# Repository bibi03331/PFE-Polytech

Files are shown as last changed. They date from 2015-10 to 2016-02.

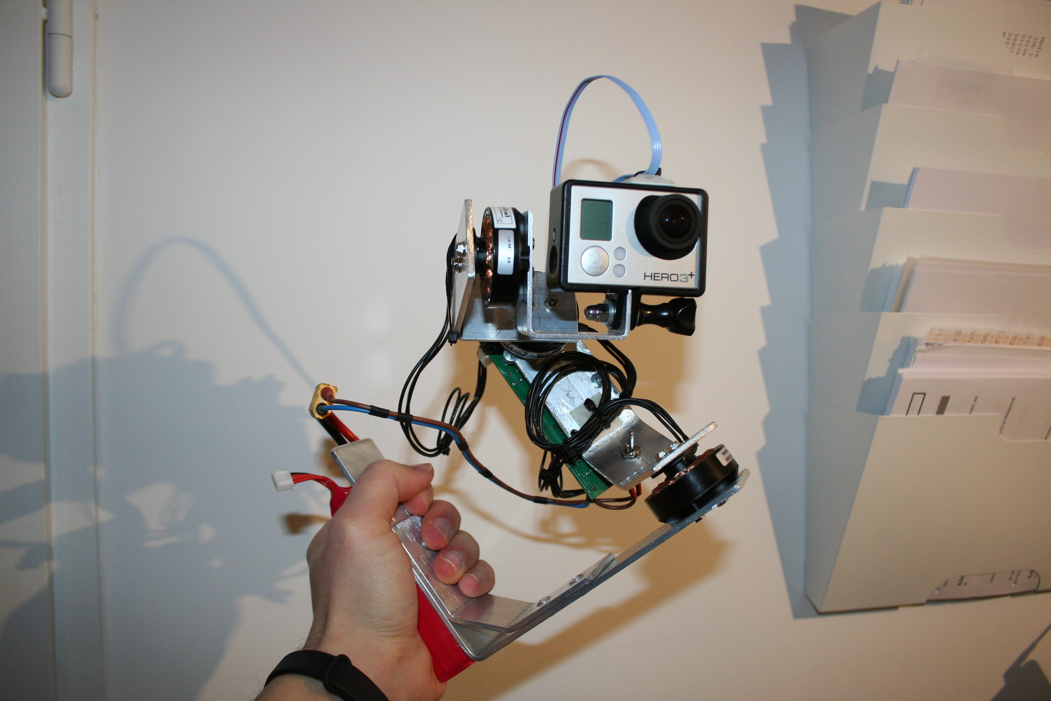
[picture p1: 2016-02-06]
Photos/Prototype final/IMG_9542.JPG

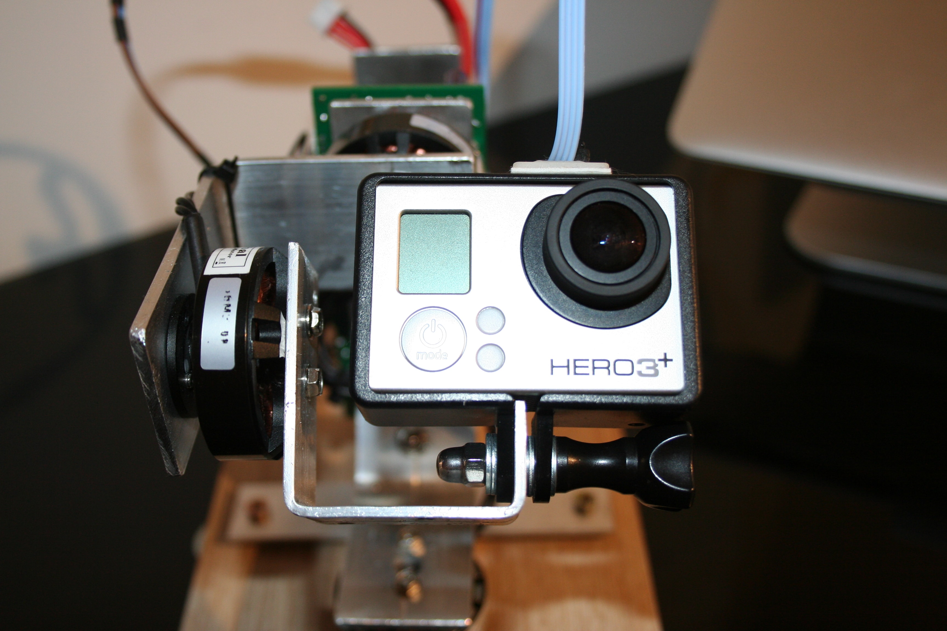
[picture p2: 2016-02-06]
Photos/Prototype final/IMG_9550.JPG

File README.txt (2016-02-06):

-------------------------------------------------------------
------------------ Projet de fin d'étude --------------------
------- Système de stabilisation motorisé pour caméra -------
-------------------------------------------------------------
       Réalisé par Sébastien Laporte à Polytech Tours
    Formation Informatique Industrielle par apprentissage
-------------------------------------------------------------

À la racine de ce dossier se trouvent l'ensemble des
livrables du projet.

  - Utilisateur : Un guide utilisateur est disponible dans
  ce dossier pour l'utilisation du système.

  - Administrateur : L'administrateur du système intervient
  pour ajuster les paramètres du système. Ce travail est
  nécessaire uniquement pour ajuster les paramètres en cas
  de modification de la structure mécanique, du type de
  moteur ou du type de caméra. Il a à sa disposition un
  guide administrateur et le code source du projet dont il
  aura besoin pour flasher à nouveau le programme dans le
  microcontrôleur avec les nouveaux paramètres

  - Développeur : Le développeur dispose de l'ensemble des
  codes sources mis à sa disposition dans le répertoire
  "Developpement" ainsi qu'un guide développeur.

-------------------------------------------------------------
==> Dossier "Developpement"
    Contient le programme du projet ainsi que l'ensemble des
    programmes réalisés au cours de ce projet.
=====> Dossier "Prototype initial"
       Contient les programmes Arduino réalisés au cours de
       la première partie du projet.
=====> Dossier "Prototype final"
       Contient les programmes Arduino réalisés au cours de
       la seconde partie de projet. Ils ont permis la
       réalisation et les tests pour le prototype final
=====> Dossier "Livrables"
       Contient les programmes Arduino mis en oeuvre pour
       la validation de chaque fonction tout au long du
       projet (Prototype initial et final). Ce dossier
       contient également la version finale du code et le
       répertoire pour la cross-compilation.
       Lien pour la mise en place de l'environnement de
       développement :https://www.pjrc.com/teensy/gcc.html
-------------------------------------------------------------

-------------------------------------------------------------
==> Dossier "CAO_mecanique"
    Contient les fichiers de conception mécanique de la
    structure et des éléments de protection.
=====> Dossier "Schémas"
       Contient les 3 schémas de la structure avant CAO
=====> Dossier "Plans et photos"
       Contient les mises en plan de chaque pièce du système
       ainsi que les aperçus des rendus 3D
=====> Dossier "Pièces"
       Contient les fichiers SolidWorks de chaque pièce
=====> Dossier "Impression 3D"
       Contient les fichiers .STL pour l'impression des
       boitiers de protection
-------------------------------------------------------------

-------------------------------------------------------------
==> Dossier "CAO_electronique"
    Contient les fichiers de conception électronique réalisés
    sous Multisim.
=====> Dossier "PDF"
       Contient le schéma de principe et les différentes
       couches du Typon
-------------------------------------------------------------

-------------------------------------------------------------
  ==> Dossier "Photos"
      Contient les photos réalisées au cours de la
      réalisation du projet
-------------------------------------------------------------

-------------------------------------------------------------
  ==> Dossier "Datasheets"
      Contient les datasheets des composants électroniques
      utilisés pour la partie électronique.
-------------------------------------------------------------

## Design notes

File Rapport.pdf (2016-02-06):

1

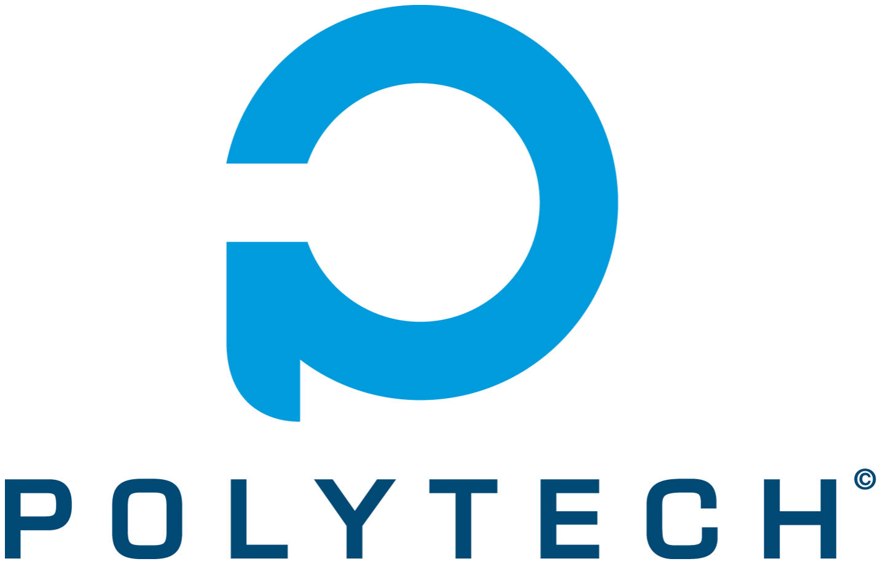
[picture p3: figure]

### École Polytechnique de l’Université de Tours

64, Avenue Jean Portalis
37200 TOURS, France
Tél. +33 (0)2 47 36 14 14

## www.polytech.univ-tours.fr

# Département Informatique industrielle

# Rapport de projet

Projet : | Système de stabilisation motorisé pour caméra
Réalisé par : | Sébastien LAPORTE | Encadré par : | Ameur SOUKHAL
Début du projet : | 22/09/2015 | Fin du projet : | 10/02/2015

Historique des modifications

Version | Date | Note de version
1.0 | 5/02/2016 | Version de dépôt initial

2

# Remerciements

Je tiens tout d’abord à remercier mon tuteur, Monsieur Ameur Soukhal pour ses conseils, et m’avoir suivi tout au long de ce projet de fin d’études.

Je remercie également les membres du service informatique de Polytech Tours et tout particulièrement Sébastien Beaufils pour sa disponibilité et son investissement. Monsieur Mayaud pour son aide et ses conseils avisés sur la réalisation de la partie mécanique du prototype. Monsieur Gaucher pour des conseils qu’il m’a apporté sur les technologies de capteurs.

Je tiens également à remercier l’ensemble des personnes qui ont contribué à la finalisation de ce rapport et de l’ensemble des documents établis.

Enfin, je tiens à remercier ma compagne pour avoir supporté de transformer ponctuellement la cuisine de notre appartement en atelier de soudure, de découpe et de perçage.

3

### Table des matières

4

## 1. Introduction

Ce document est un bilan de projet de fin d’études à Polytech Tours. Il a pour objectif de faire le lien entre les différents documents et livrables réalisés au cours de ce projet, d’exposer et justifier les choix qui ont été faits et d’effectuer un bilan sur le déroulement du projet.
Le porteur du projet qui agit également en tant que MOE est Sébastien Laporte, étudiant en cinquième année de cycle d’ingénieur en informatique industrielle. L’encadrant du projet représentant la MOA est Monsieur Ameur Soukhal, enseignant-chercheur au CNRS.
Le sujet du projet est la réalisation d’un système de stabilisation motorisé pour une caméra d’action sur trois axes.

## 1.1. Contexte du projet

Depuis quelques années, le marché des caméras d’action est en constante évolution. C’est la marque GoPro qui a démocratisé ce type de matériel et qui s’est imposée comme leadeur dans le domaine. Grâce à cette gamme de caméras, il est possible de filmer ses activités sportives, sur tous les terrains avec un minimum d’encombrement. Cependant, malgré la miniaturisation et la qualité du capteur, il est souvent difficile de filmer de manière stable lorsqu’on conduit une moto ou que l’on descend une piste de ski. C’est donc dans ce contexte que la MOA a proposé ce projet afin de trouver une solution à ce besoin.

## 1.2. Objectif

L’objectif de ce projet était de concevoir et réaliser un système de stabilisation pour caméra d’action. Fixée sur le système, la caméra sera stabilisée de façon mécanique pour permettre à l’utilisateur de filmer tout en conservant une image stable. Cette stabilisation sera assurée par des effecteurs électriques. Sont utilisation se devait simple et intuitive.

## 1.3. Existant

Certains projets ont vu le jour avec la prolifération des drones pourvus de caméras sur nacelles stabilisées. Le choix qui a été pris dans le cadre de ce projet est de considérer que le projet n’a pas d’existant ni matériel ni logiciel. En effet, dans le cadre pédagogique de ce projet, l’objectif était de se confronter à l’ensemble des problématiques mécaniques, électroniques et logicielles.

## 2. Cahier des charges

L’objectif du projet est de réaliser un système de stabilisation motorisé et autonome pour caméra. Usuellement appelé « Steady cam » pour « Steady camera », ce type de matériel est utilisé notamment dans le cinéma pour réaliser des travelings fluides en absorbant les mouvements parasites. Le système doit permettre d’assurer la stabilisation de caméras d’action type GoPro.
Contraintes du projet
- Le système doit être énergétiquement autonome
- La stabilisation doit se faire sur au moins deux axes : Roll + Pitch
- Effort de conception : Prototype avec un faible poids et encombrement
- L’utilisateur doit avoir la possibilité d’ajuster les paramètres d’amortissement

Livrables attendus
- Cahier de spécification
- Document d’analyse et modélisation
- Documentation de reprise de projet (Guide utilisateur, administrateur et développeur)
- Prototype fonctionnel

5

## 3. Problématique

Pour répondre aux spécifications qui ont été établies, nous avons établi la problématique suivante afin d’identifier les principales contraintes de ce système.
- Énergétiquement autonome
Le système doit être alimenté par batterie pour permettre à l’utilisateur de pouvoir l’utiliser sans contrainte d’alimentation secteur. Il est également nécessaire de prendre en compte le besoin important en courant pour l’alimentation de trois moteurs de façon simultanée.
- Réactivité
Destiné à stabiliser une caméra pour effectuer des prises de vue, le système doit être très réactif pour effacer les mouvements parasites induits par son utilisateur. Il est donc nécessaire d’avoir un traitement de l’information rapide, mais aussi d’avoir des effecteurs électriques suffisamment réactifs.
- Évolutivité
Dans le but de pouvoir modifier la structure mécanique pour l’adapter à un autre appareil de prise de vue, la partie électronique et la partie logicielle doivent être conçues pour s’adapter à ce changement. Cette contrainte implique un bon dimensionnement pour la partie électronique et une conception modulaire du programme afin de prévoir ces changements.
- Encombrement
Comme indiqué dans le cahier des charges, le système doit être le plus contenu possible afin de pouvoir être embarqué sur une moto, ou tenu à la main sans être une contrainte pour son utilisateur. Pour cela, un effort doit être fait sur la partie mécanique pour concevoir une structure la plus minimale possible. De plus, la partie électronique doit être parfaitement intégrée au système et respecter les mêmes dimensions que la structure.
- Robustesse
Enfin, la robustesse est un élément important à considérer. En effet, le produit doit être utilisable dans des conditions normales d’utilisation et doit être durable dans le temps. Cela implique une structure mécanique solide, des moteurs légèrement surdimensionnés ainsi qu’une protection des parties électroniques.

## 4. Conduite de projet

Pour mener à bien ce projet, nous avons dû sélectionner une méthode de gestion de projet. Ensuite, nous avons effectué un découpage des tâches pour réaliser un planning prévisionnel.
Notre choix de méthode s’est porté sur la méthode SCRUM des méthodes AGILE. En effet, étant sur des technologies que nous ne connaissions pas, le fait d’ajouter des fonctionnalités au système au fur et à mesure de l’avancement nous paraissait parfaitement adapté à ce projet.

## 4.1. Méthodologie

Comme présenté dans le livrable « Cahier de spécifications », nous avons organisé le projet en deux sous-projets. Cette décision a été faite après une étude de faisabilité au cours de laquelle nous avions identifié les risques. Le risque majeur de ce projet a été identifié comme l’obtention de l’orientation du capteur dans l’espace. En effet, aujourd’hui ces capteurs d’orientation intégrant un accéléromètre, un gyroscope et éventuellement un magnétomètre se trouvent dans tous les smartphones et tablettes du marché. Malgré le fait que ces capteurs soient très rependus, il y a encore très peu d’algorithmes Open Source permettant d’exploiter ces données. C’est pourquoi nous avons choisi dans un premier de nous consacrer à l’acquisition et au traitement des données sur un premier prototype. Puis, dans une deuxième phase du projet, après validation du fonctionnement de ces fonctionnalités de base,

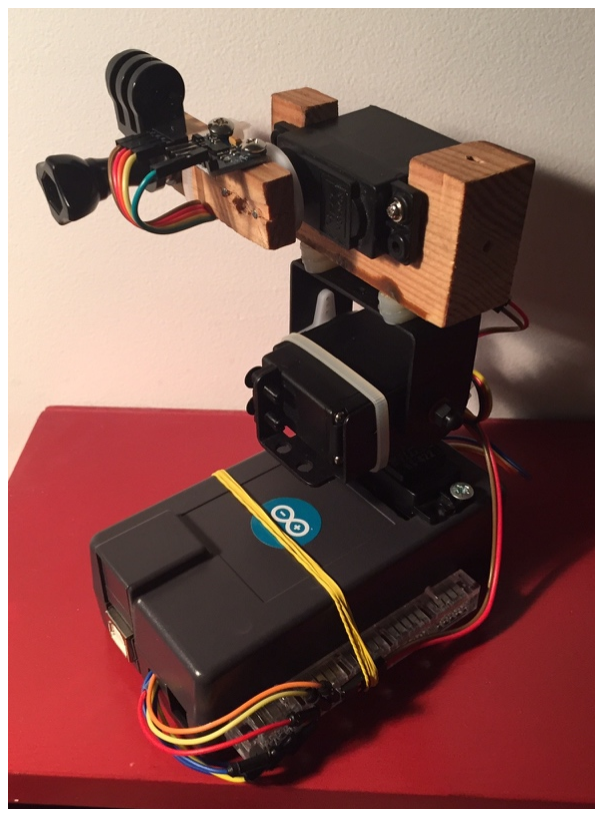
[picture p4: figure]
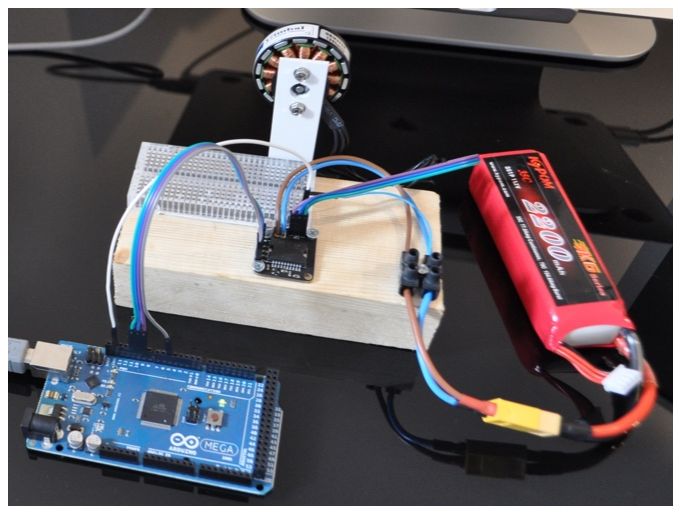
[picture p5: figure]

6

nous avions prévu de créer le prototype final, répondant à l’ensemble de la problématique et des exigences exprimées dans le cahier des charges.
- Prototype initial
Pour commencer le projet, nous avons choisi de nous
concentrer sur la prise en main du capteur et le traitement associé en mettant de côté la commande des moteurs brushless. Pour effectuer des tests, nous avons mis en place un prototype équipé de trois servomoteurs de modélisme pour remplacer les moteurs. En effet, la commande de ce type d’effecteur est grandement simplifiée par l’utilisation des librairies Arduino.
Ce premier prototype a permis de mettre en œuvre :
- La configuration du capteur
- De comprendre et d’implémenter un algorithme permettant d’effectuer la calibration du capteur
- D’implémenter un algorithme de filtre PID
- De tester plusieurs techniques de fusion de données d’un tel capteur
- De valider le fonctionnement du prototype sur deux axes : Roll et Pitch
Après la validation de fonctionnalités, nous avons réalisé
des vidéos pour valider le fonctionnement auprès de la
MOA :
- Prototype initial sur deux axes : https://www.youtube.com/watch?v=oEspsLbolnE
- Ajout de l’axe Z (Yaw) : https://www.youtube.com/watch?v=FzccmuE41do
- Prototype initial sur trois axes : https://www.youtube.com/watch?v=J3hMNFk_600

Dans cette première partie, nous avons également
réalisé un banc d’essai moteur pour prendre en
main la commande de ce type de moteur brushless et implémenter la fonction permettant la commande.
Pour réaliser la commande du moteur, nous avons utilisé une Breadboard intégrant le composant L6234 afin de concentrer le travail sur l’implémentation de la fonction au niveau du microcontrôleur. La partie électronique sera mise en œuvre pour le prototype final.
Le fonctionnement de la commande d’un moteur
brushless a également été validé avec un vidéo
comme livrable. Celle-ci montre le fonctionnement du moteur avec variation de la vitesse : https://www.youtube.com/watch?v=QIOnZgU_zDE À la fin de cette première partie du projet, nous avions mis en œuvre l’ensemble des techniques nécessaire à la réalisation du prototype final.

Figure 1 : Prototype initial

Figure 2 : Banc d'essai moteur

7

- Prototype final
La seconde partie du projet a pour objectif de capitaliser les connaissances et techniques développées lors de la première partie du projet pour les intégrer dans un prototype final. Dans cette partie du projet, nous avions donc toutes les connaissances nécessaires à la conception et à la réalisation du système.
Lors de cette phase, nous avons effectué la conception de la carte électronique, la conception mécanique et le code optimisé pour le microcontrôleur sélectionné pour le prototype final.

## 4.2. Découpage en tâches

Le découpage en tâches a été réalisé dans la partie 8 du livrable « Cahier de spécifications ».

## 4.3. Choix stratégiques

Au cours du projet, nous avons dû effectuer des choix techniques qui sont liés à la gestion de projet.
- Choix de l’algorithme de fusion des données du capteur
Pour obtenir l’orientation d’un solide dans l’espace il existe plusieurs types de capteurs. Dans le cadre de ce projet, nous avions établis lors de la phase de spécification d’utiliser un accéléromètre, un gyroscope et un magnétomètre. Pour obtenir l’orientation du solide, il est nécessaire de fusionner ces valeurs afin d’obtenir par exemple une représentation d’Euler. Lors de nos recherches, nous avions observé qu’il existe essentiellement deux méthodes pour obtenir l’orientation avec le capteur mPU-9250 :
- Soit utiliser le DMP (processeur spécialisé dans le calcul intégré au capteur). Cette Solution permet d’obtenir de manière simple et précise l’orientation du capteur.
- Soit mettre en œuvre un algorithme au niveau du microcontrôleur en récupérant les valeurs brutes des différents capteurs. Cette solution nécessite l’utilisation d’un algorithme mathématique déjà existant, car cela requiert de grandes compétences très spécialisées.
La solution avec l’utilisation du DMP n’a pas été retenue du fait de devoir flasher à chaque démarrage du système le code binaire d’un programme propriétaire dans le DMP. En effet, nous avions comme volonté de maitriser l’ensemble des fonctions que nous utilisons pour ce projet. Nous avons donc choisi d’implémenter l’algorithme de Madgwick au niveau du microcontrôleur. Nous verrons par la suite que ce choix n’a pas permis d’aboutir à une solution pleinement satisfaisante en terme de performances.
- Choix sur la structure mécanique
De nombreuses structures avec moteur brushless intégrés sont en vente dans des boutiques spécialisées ou sur internet. Ces Structures sont destinées à être utilisées sur des drones pour stabiliser des caméras d’action. Ce type de matériel aurait très bien pu convenir pour ce projet. Néanmoins, ayant des connaissances en conception mécanique, nous avions comme volonté de réaliser nous même l’ensemble dans la partie mécanique.
- Choix sur la partie électronique
Comme pour la partie mécanique, le marché des drones a fait apparaitre des cartes électroniques intégrant un microcontrôleur, des drivers de moteurs brushless sur une même carte pour un encombrement et un prix très réduit. Là encore, nous souhaitions réaliser nous même notre propre carte électronique afin de nous confronter aux différentes problématiques induites par ce type de projet.

8

## 4.4. Planification

La gestion du planning établie en début de projet (voir cahier de spécification, partie 10) a été suivie à quelques exceptions en fin de projet en raison de tests non satisfaisants sur une tâche du projet qui nous a contraints à revenir sur l’implémentation d’une fonction. Certaines tâches non prioritaires n’on donc pas pût être réalisées :
- Réalisation du code natif pour la fonction « Commande de l’orientation »
- Intégration du code natif pour le prototype final
Nous avions environ 120h dédiées sur notre emploi du temps pour la réalisation du PFE. Pour mener à bien ce projet, nous avons consacré entre 470 et 500 heures ce qui totalise un minimum de 450 heures sur le temps personnel. Cet investissement personnel nous a permis de ne pas prendre de retard sur le planning que nous nous étions fixé.

## 4.5. Livrables du projet

Ce rapport est accompagné de plusieurs livrables détaillants les spécifications et l’analyse qui a été faite pour ce projet. Les guides doivent permettre une reprise du projet par niveau d’utilisateur.
- Cahier de spécifications
Ce document a pour objectif de définir les besoins, l’environnement et les objectifs pour la réalisation du projet. Il contient le découpage des tâches ainsi que la planification.
- Document d’analyse et modélisation
Ce document a pour objectif d’expliquer en détail les choix et solutions mises en place pour la réalisation du projet de fin d’études. Ce rapport est organisé en plusieurs sous-parties : Électronique, mécanique et logicielle.
- Guide de l’utilisateur
Ce document est destiné à l’utilisateur du système. Il décrit les démarches à suivre pour l’utilisation du système.
- Guide l’administrateur
Ce document est destiné à l’administrateur du système. Il décrit les démarches à suivre pour la configuration du système. Les configurations présentées dans ce document doivent être effectuées par l’administrateur pour préparer le système après sa fabrication. Ce paramétrage est à effectuer une seule fois dans la vie du système. Ce document peut être également utile aux développeurs.
- Guide du développeur
Ce document est destiné à décrire l’architecture du code et présente les différents codes sources associés au projet.
- Code source du projet
Ce projet est livré avec le code source et son environnement nécessaire à la cross-compilation.
- Codes exemples associés au projet
L’ensemble des codes sources des programmes utilisés au cours de la vie du projet est également inclus dans les livrables du projet. Ils sont décrits dans le guide du développeur.

9

## 5. Schéma général du système

Le schéma ci-dessous permet de définir le nom des axes que nous avons utilisé dans l’ensemble des rapports et documents fournis. Il permet également de définir le repère géométrique.

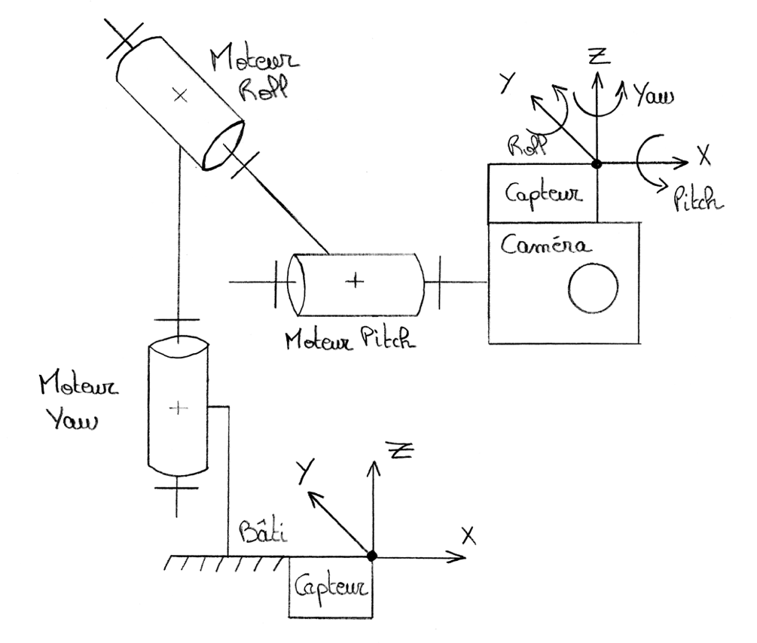
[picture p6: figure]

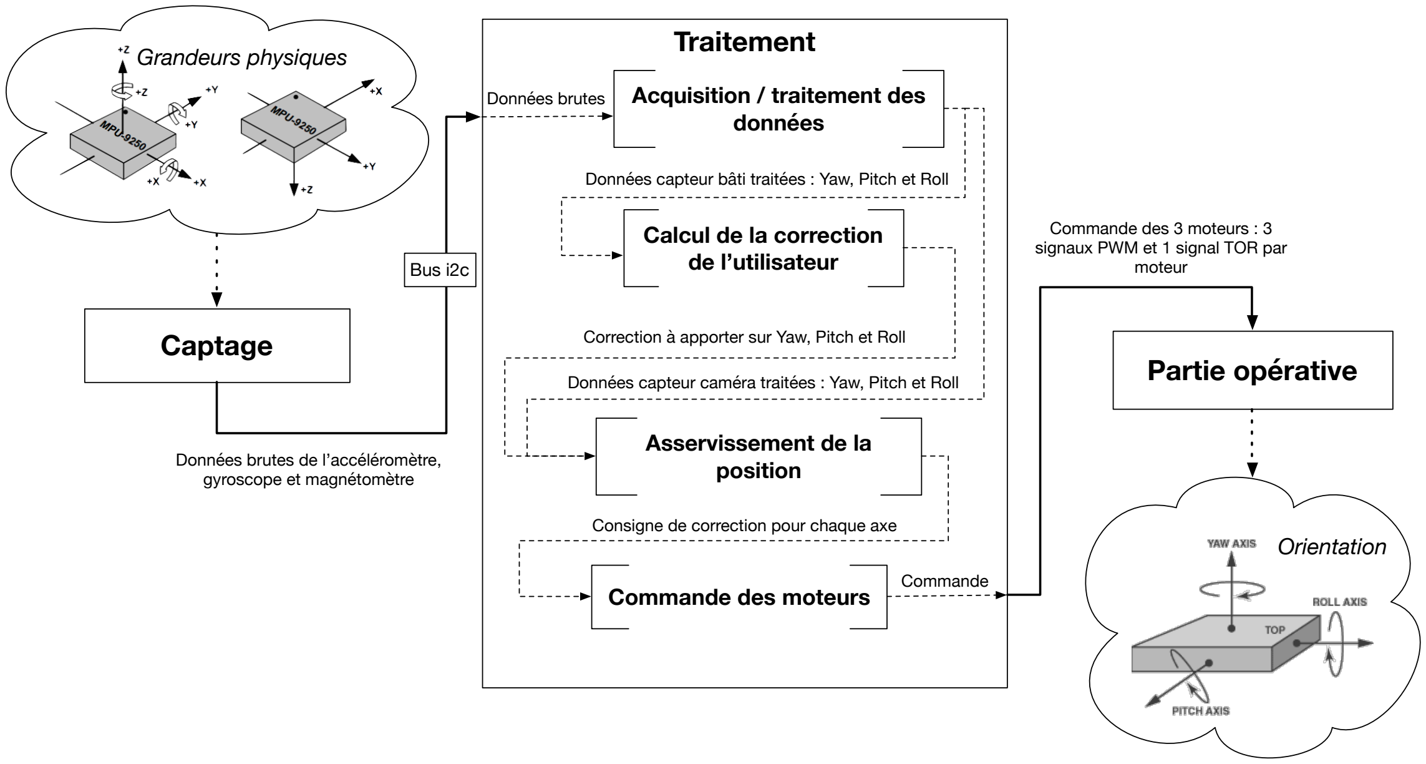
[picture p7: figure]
Captage; Traitement; Acquisition / traitement des données; Asservissement de la position; Commande des moteurs; Partie opérative; Grandeurs physiques; Bus i2c; Données brutes de l’accéléromètre, gyroscope et magnétomètre; Consigne de correction pour chaque axe; Données brutes; Commande; Commande des 3 moteurs : 3 signaux PWM et 1 signal TOR par moteur; Orientation; Calcul de la correction de l’utilisateur

10

## 6. Architecture mise en œuvre

Pour réaliser la fonction de stabilisation de la caméra, nous avons découpé le système en trois sous-parties : Captage, Traitement et partie opérative.

Figure 4 : Architecture du système
Ø Captage : Sous-ensemble permettant de fournir au système les données brutes nécessaires à la modélisation de l’orientation de la caméra et du système dans un espace 3D. C’est grâce à l’orientation de la caméra que nous effectuons l’asservissement en position.
Ø Traitement : Sous-ensemble permettant de réaliser plusieurs fonctions : Traitement des données, calcul de la correction de l’utilisateur, asservissement en position et commande des moteurs.
- Fonction « Acquisition / traitement des données » : Permets d’obtenir l’orientation exacte de la caméra et du bâti à partir des données brutes envoyées par le sous-ensemble « Captage ».
- Fonction « Calcul de la correction de l’utilisateur » : Cette fonction permet de calculer la correction à apporter pour modifier l’orientation de la caméra en fonction de celle du bâti.
- Fonction « Asservissement de la position » : Permets de calculer la correction à appliquer sur le sous-ensemble « Partie opérative » pour corriger l’orientation de la caméra en fonction des données produites par la fonction « Traitement des données ».
- Fonction « Commande des moteurs » : Permets d’effectuer la commande des moteurs en fonction de la consigne calculée par la fonction « Asservissement de la position ».
Ø Partie opérative : Sous-ensemble constitué d’une structure mécanique et de moteurs permettant d’orienter la caméra dans un espace 3D.

Données capteur caméra traitées : Yaw, Pitch et Roll

Données capteur bâti traitées : Yaw, Pitch et Roll

Correction à apporter sur Yaw, Pitch et Roll

11

## 7. Matériel utilisé

Le choix et la justification des composants du système a été réalisé dans le livrable « Analyse et modélisation » dans la partie 4.1. La liste de matériel qui suit concerne le matériel nécessaire à la réalisation du prototype final. Au cours du projet, un premier prototype à été réalisé qui sera décrit dans la partie gestion de projet.
Le tableau ci-après fait une synthèse du matériel qui a été nécessaire à la réalisation électronique.
Désignation | Quantité | Prix unitaire TTC
Capteur MPU-9250 | 1 | 11,90€
Moteur brushless BLDC GBM3508-130 | 3 | 24,43€
Microcontrôleur Teensy 3.1 | 1 | 19,80€
Batterie LIPO 3S 2200 mAh | 1 | 23,90€
Régulateur LM2574 | 3 | 7,80€
Support DIP20 | 3 | 1,03€
Condensateur chimique 22 uF | 1 | 0,50€
Condensateur chimique 220 uF | 1 | 0,80€
Condensateur céramique 100 nF | 3 | 0,10€
Condensateur chimique 100 uF | 3 | 0,50€
Condensateur céramique 220 nF | 3 | 0,80€
Diode Schottky MBR160G | 1 | 0,20€
Bobine 330 uH | 1 | 1,00€
Condensateur céramique 10 nF | 3 | 0,10€
Condensateur céramique 1 uF | 3 | 0,10€
Diode 1N4148 | 6 | 0,10€
PCB Eurocircuit | 1 | 71,91€
Interrupteur 2 positions | 1 | 2,90€
Total TTC | 238,39€

Le tableau ci-après constitue la la liste du matériel pour la réalisation de la partie mécanique.
Désignation | Quantité | Prix TTC
Plat aluminium brut (Longueur 1 m – Largeur 35 mm) | 1 | 7,45€
Plat aluminium brut (Longueur 1 m – Largeur 20 mm) | 1 | 5,90€
Vis M3 15 mm à tête cylindrique + écrous + rondelles | 4 | 2,00€
Vis M3 5 mm à tête plate | 9 | 2,00€
Fixation GoPro « The Frame » | 1 | 9,90€

Coût total du projet en matériel : 265,64€

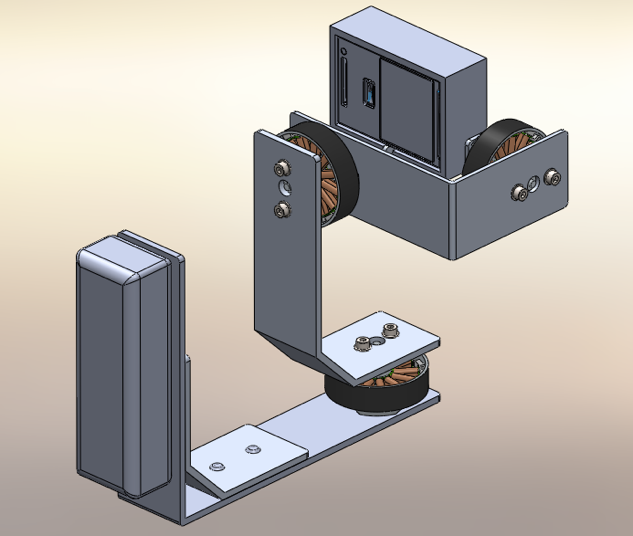
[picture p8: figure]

12

## 8. Conception et réalisation

## 8.1. Conception de la structure

Afin de réaliser la structure mécanique, nous avons réalisé dans un premier temps un schéma permettant de définir les éléments de la structure.

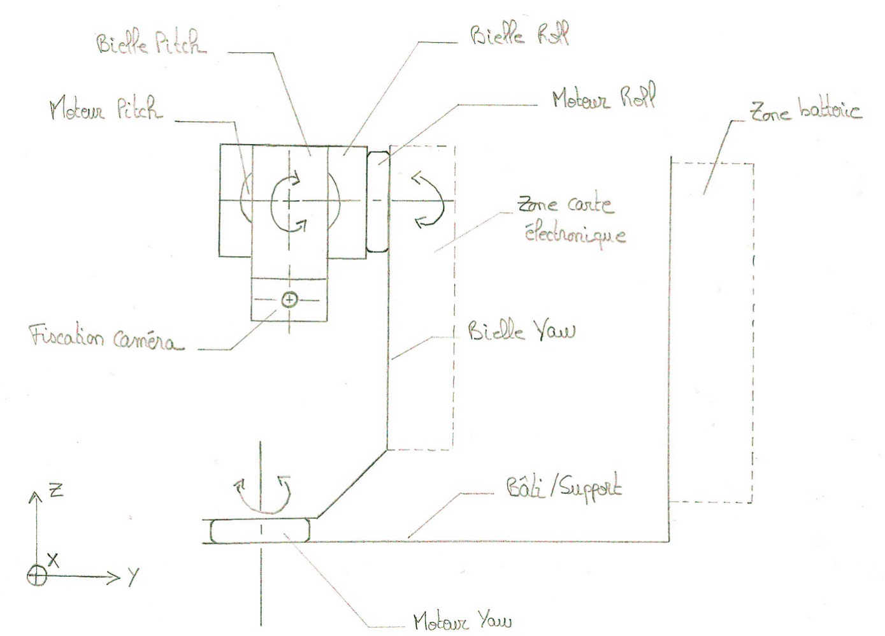
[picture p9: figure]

Figure 5 : Schéma de la structure mécanique
Nous avons ensuite entrepris une phase de conception sur ordinateur à l’aide du logiciel SolidWorks pour obtenir un 3D. Cela a également permit de définir les dimensions exactes de chaque pièce et de s’assurer qu’il n’y a pas de collisions entre les différents éléments. Les plans de l’ensemble de la structure se trouvent en annexe du document « Analyse et modélisation ».

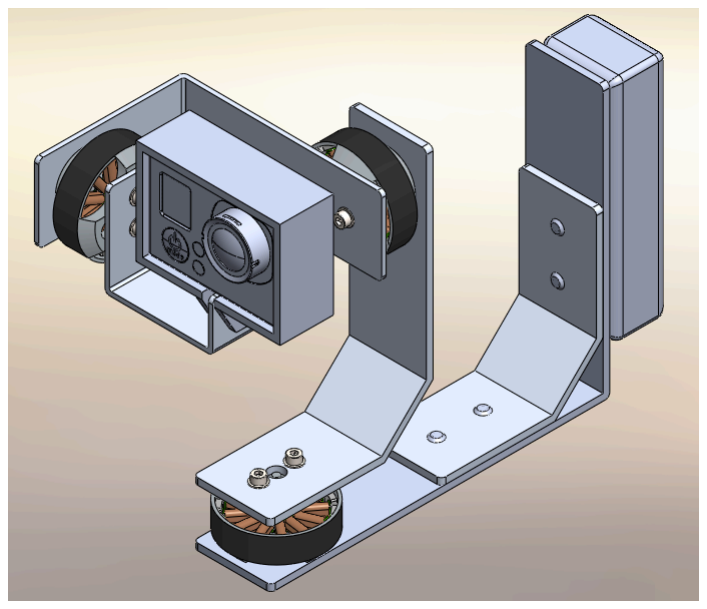
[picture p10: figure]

Figure 6 : Rendu 3D structure mécanique

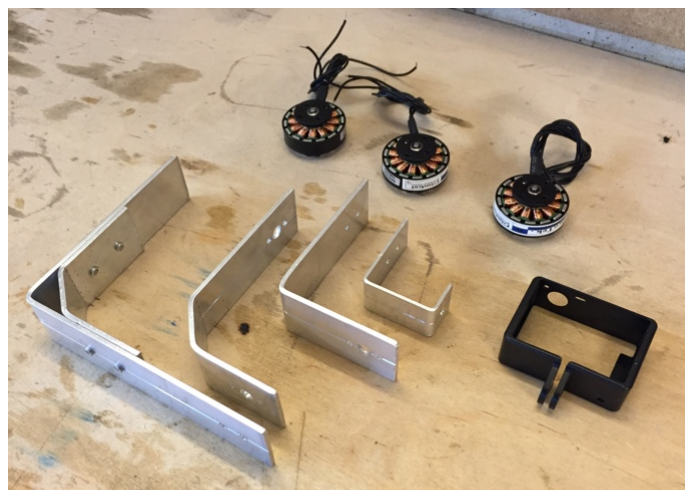
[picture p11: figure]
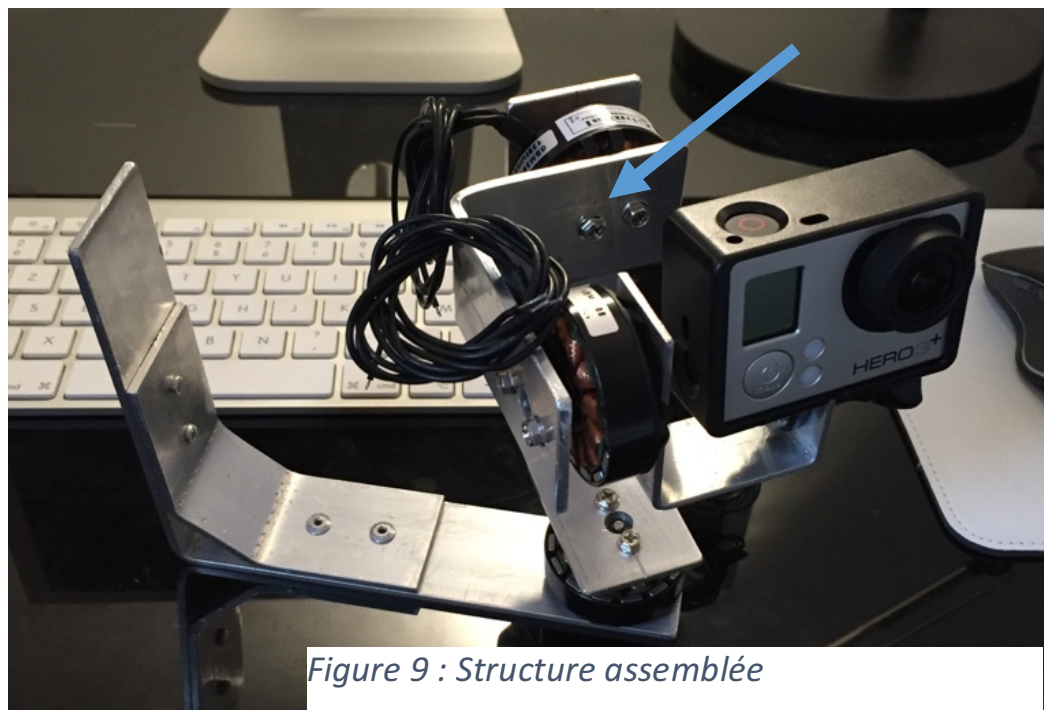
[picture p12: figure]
Figure 9 : Structure assemblée

13

## 8.2. Conception des éléments de protection

Afin de protéger la carte électronique, nous avons réalisé un boitier de protection. Nous avons effectué la conception sur ordinateur, puis réalisé les pièce grâce à une imprimante 3D.

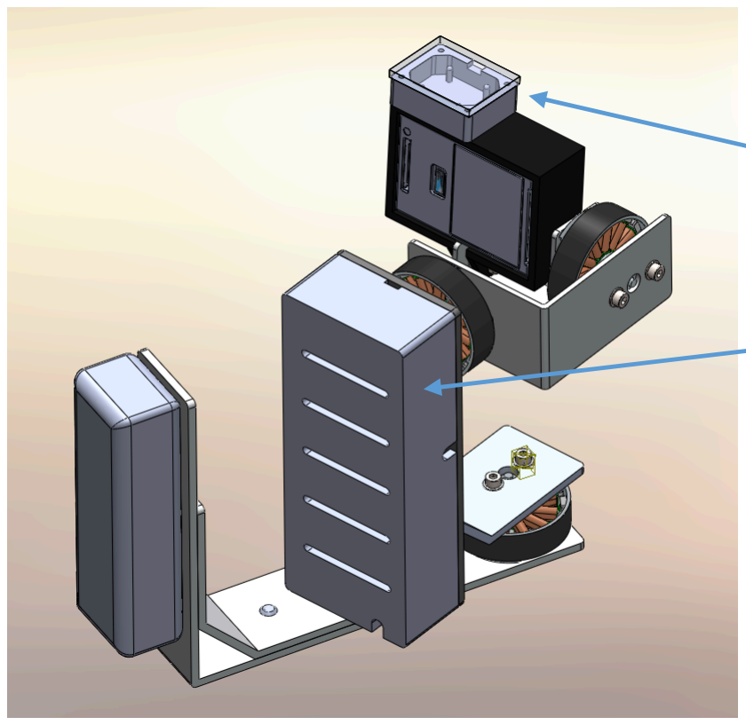
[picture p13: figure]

Figure 7 : Éléments de protection

## 8.3. Réalisation de la structure

Pour réaliser la structure mécanique, nous nous sommes appuyé entièrement sur les plans que nous avions réalisé pour chaque pièce grâce à la modélisation 3D. En procédant ainsi, nous avions l’assurance de réaliser les pièces avec les bonnes dimensions.
Cependant, lors de la modélisation nous n’avions pas les compétences nécessaires pour prendre en compte le poids de la caméra pour calculer le point d’équilibre de la structure.

En effet, comme on le voit sur l’illustration ci-contre, le système est en équilibre, même sans l’aide des moteurs. Cela permet d’éviter aux moteurs d’appliquer un effort lorsque le système est parfaitement à l’horizontal. Nous avons donc dû adapter la dimension de la bielle pointée par la flèche sur l’illustration afin d’obtenir le résultat suivant.

Boitier de protection du capteur

Boitier de protection de
la carte électronique

Figure 8 : Réalisation de la structure

## 8.4. Partie électronique

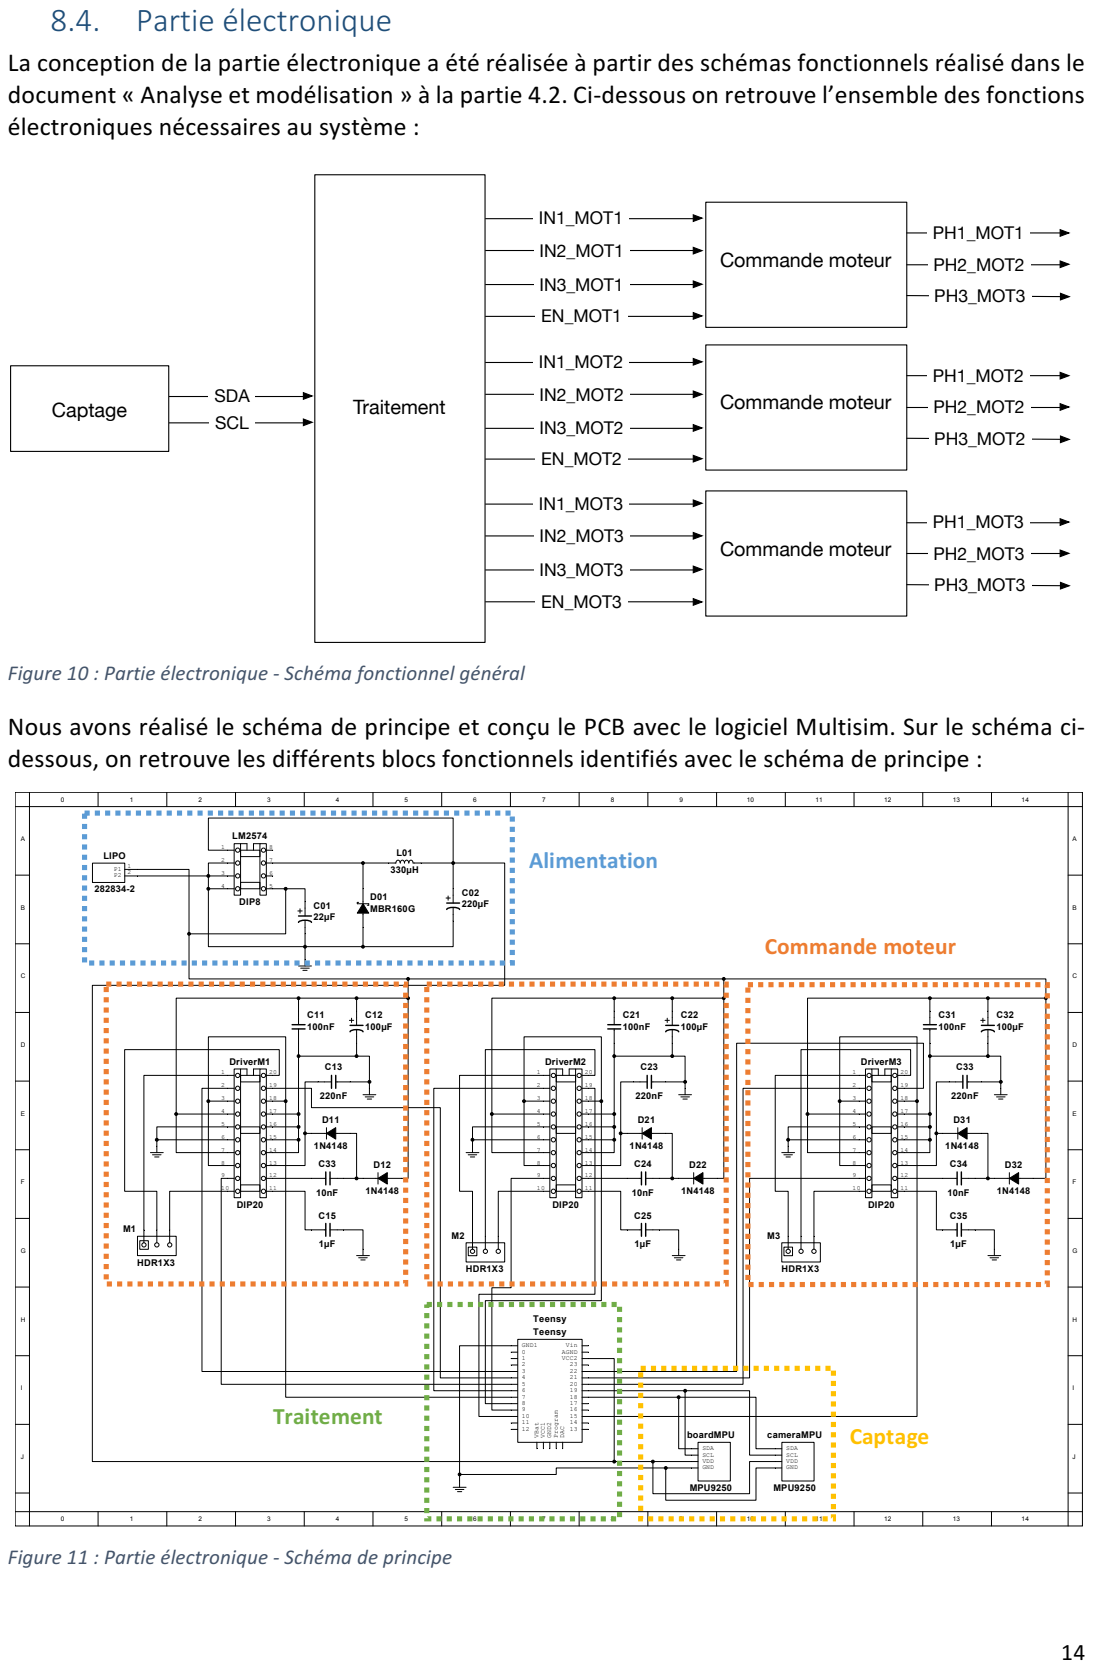
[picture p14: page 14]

La conception de la partie électronique a été réalisée à partir des schémas fonctionnels réalisé dans le
document « Analyse et modélisation » à la partie 4.2. Ci-dessous on retrouve l’ensemble des fonctions
électroniques nécessaires au système :

Figure 10 : Partie électronique - Schéma fonctionnel général
Nous avons réalisé le schéma de principe et conçu le PCB avec le logiciel Multisim. Sur le schéma ci-
dessous, on retrouve les différents blocs fonctionnels identifiés avec le schéma de principe :

Figure 11 : Partie électronique - Schéma de principe

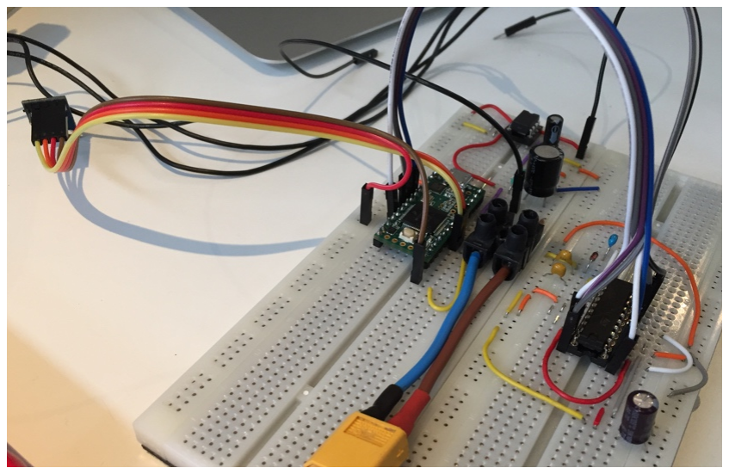
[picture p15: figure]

15

Pour valider cette conception que nous avions réalisée en nous appuyant sur les datasheet des composants, nous avons utilisé une platine de développement reproduit chaque fonction.
Ainsi, nous avons pu valider chaque
fonction | électronique
indépendamment en réalisant un
programme | de | test | sur | le
microcontrôleur. Après la validation de chaque fonction, nous avons effectué un test avec l’ensemble des
fonctions pour nous assurer qu’il n’y
a pas d’effet de bords.
La contrainte principale pour la conception de la carte électronique était l’encombrement. En effet, nous devions contenir au maximum les dimensions du PCB pour qu’il puisse être fixé sur le système sans gêner l’utilisateur.

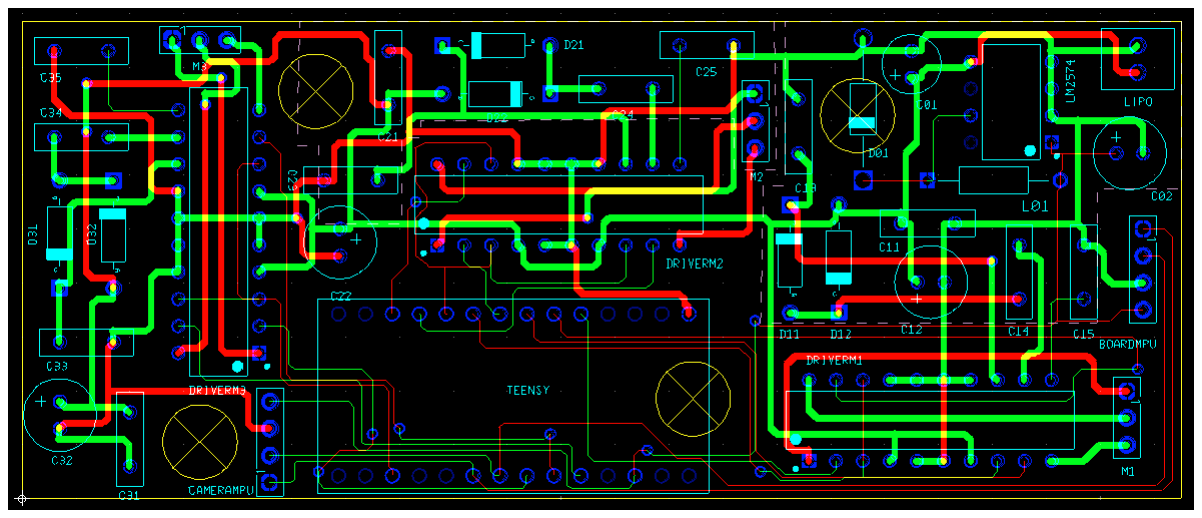
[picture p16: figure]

Figure 13 : Partie électronique - Conception du PCB
Le PCB a été réalisé en 2 couches pour permettre un gain de place. Toujours dans une démarche d’optimisation, nous avons utilisé deux tailles de piste :
- Les pistes de données : 0,254 mm
- Les pistes de puissance : 0,762 mm Afin de limiter les perturbations électromagnétiques entre les pistes de puissance et les pistes de données, nous avons créé des zones « keep-out » pour éloigner au maximum de deux types de pistes. Le placement des composants a également nécessité un travail d’optimisation pour trouver l’arrangement qui permet un encombrement minimum tout en limitant les proximités de certaines pistes et en rapprochant au maximum les condensateurs de découplages des composants concernés. Le PCB a été réalisé par la société EURO circuits. Afin de supporter les forts courants induits par les moteurs, nous avons spécifié une épaisseur de piste à 35μm pour supporter les forts courants.

Figure 12 : Conception électronique - Tests

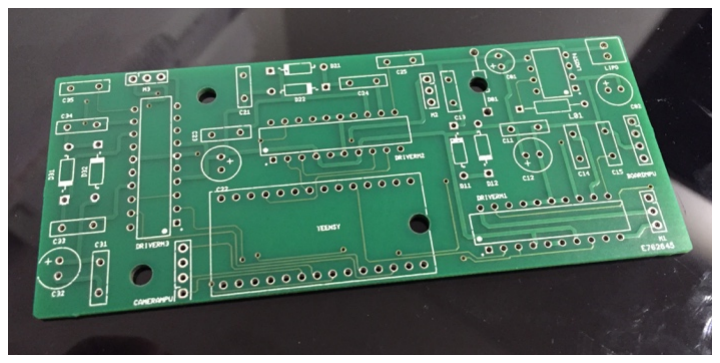
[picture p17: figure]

16

Afin de pouvoir fixer efficacement la carte électronique à la structure mécanique, nous avions prévu des trous de fixation lors de la conception du PCB.
Afin d’obtenir un PCB de qualité et de simplifier la soudure des composants, nous avons opté pour une finition « Standard Pool » ce qui permet d’avoir une carte vernie (meilleur durée
de vie) et des trous métallisés pour les
composants.
La dernière étape de pour la partie électronique à été la mise en place des composants sur le PCB et le test de chaque partie. Pour effectuer les tests, nous avons connecté les trois moteurs ainsi que le capteur à la carte et avons flashé sur le microcontrôleur un programme permettant de faire l’acquisition des données brutes du capteur tout en faisant tourner les trois moteurs.
L’ensemble des tests ont étés réalisés avec succès.

Figure 14 : Partie électronique - PCB

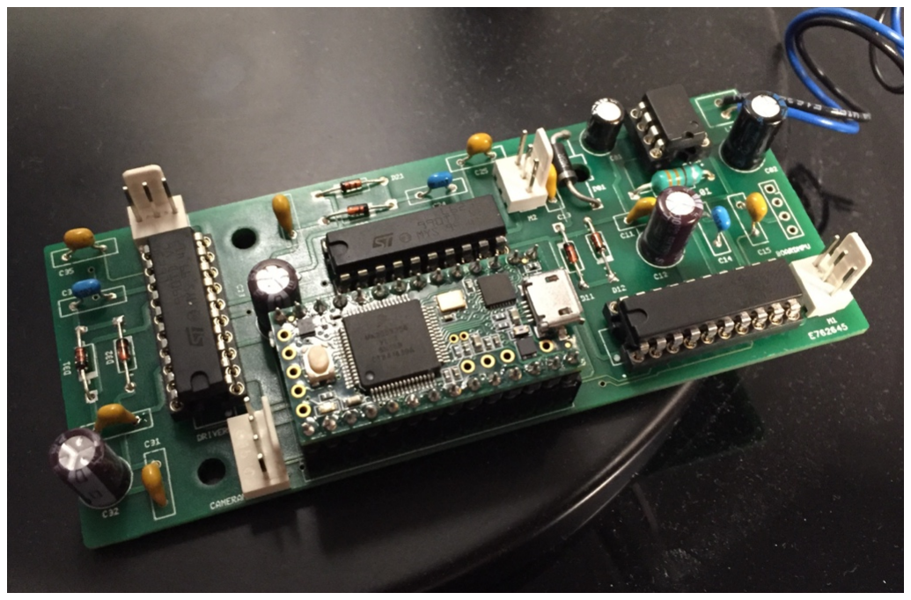
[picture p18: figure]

Figure 15 : Partie électronique - Carte électronique assemblée

17

## 8.5. Partie logicielle

Le programme du microcontrôleur est organisé en deux partie :
- Une phase d’initialisation permet de configurer le matériel, charger les paramètres et éventuellement d’effectuer l’étalonnage du capteur. Cette phase est décrite dans le document « Analyse et modélisation » dans la partie 6.5.1.
- La phase de fonction normal permet d’effectuer la stabilisation de la caméra. Le processus est constitué d’un ensemble de fonctions qui s’enchainent de façon séquentielle. Cette phase est décrite dans le document « Analyse et modélisation » dans la partie 6.5.2.
8.5.1. Phase d’initialisation du programme

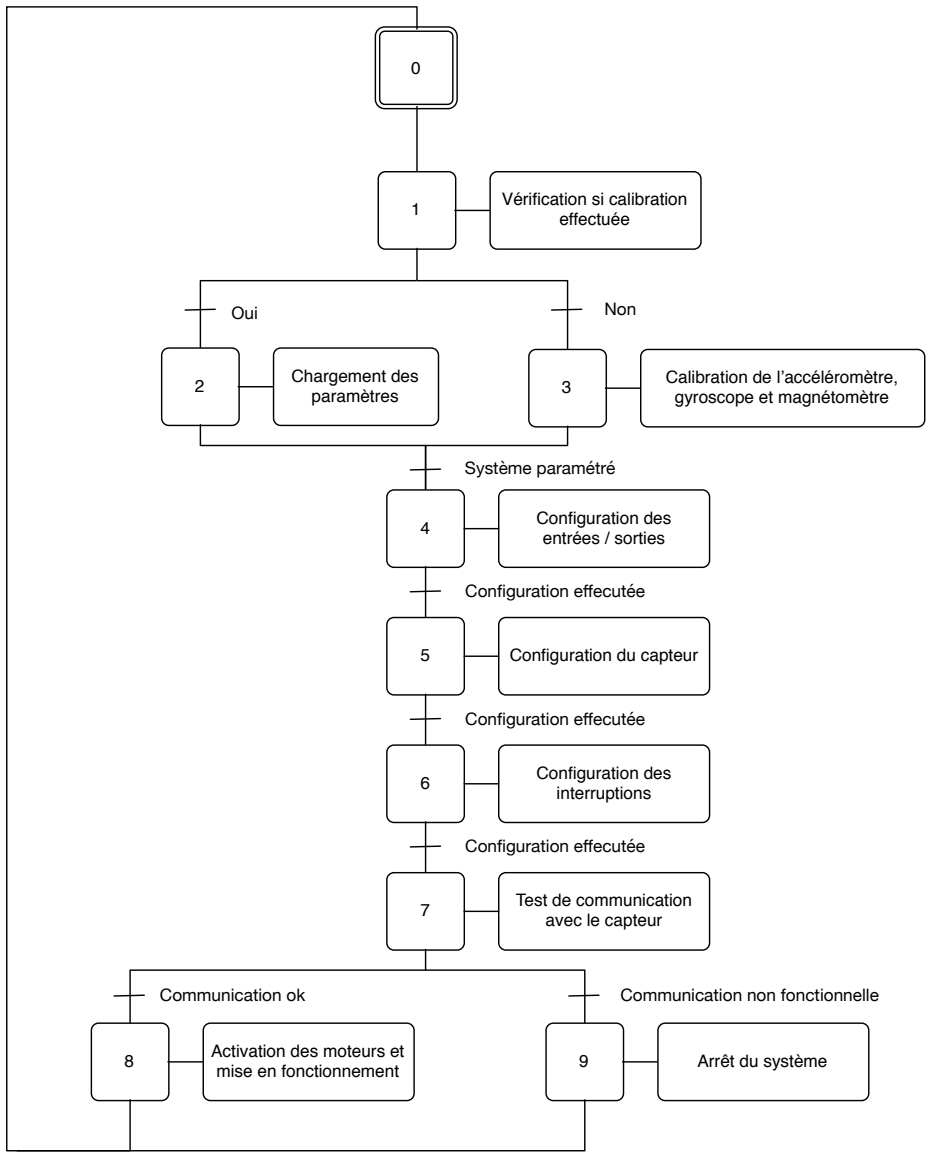
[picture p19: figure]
Vérification si calibration; effectuée; Calibration de l’accéléromètre,; gyroscope et magnétomètre 2; Chargement des; paramètres; Oui; Non; Configuration des; entrées / sorties; Configuration du capteur; interruptions; Test de communication; avec le capteur; mise en fonctionnement; Communication ok; Communication non fonctionnelle; Système paramétré; Configuration effecutée

Figure 16 : Partie logicielle - Phase d'initialisation

8 | 9 | Arrêt du système Activation des moteurs et

18

8.5.2. Phase de fonctionnement normal du programme Le processus de fonctionnement normal du programme du microcontrôleur peut être décrit par le grafcet ci-contre. Les fonctions représentées s’enchaines successivement en partant de la récupération des données brutes du capteur jusqu’à la commande de la partie opérative. Cependant, les opérations sont cadencées par des interruptions avec les fréquences suivantes :
Interruption 1 : Cadencée à 200 Hz
- Récupération des données brutes du capteur
- Conversion de la représentation quaternion en Euler

Interruption 2 : Cadencée à 50 kHz
- Application du filtre PID
- Commande de la partie opérative

Interruption 3 : Cadencée à 1 kHz
- Application du filtre de Madgwick

Pour plus de détails sur le cadencement de ces interruptions, se référer à la partie 6.5.2 du livrable « Analyse et modélisation ».

8.5.3. Configuration du capteur
Durant ce projet, une des tâches qui nous aura pris le plus de temps est la configuration du capteur. En effet, le capteur MPU-9250 est très complexe et dispose d’un grand nombre de registres pour effectuer sa configuration. De plus, sa configuration fait appel à des notions de physique que nous ne maitrisions pas en début de projet, et qui restent relativement abstraites malgré un important travail de recherche. Dans la partie 6.4.1 du livrable « Analyse et modélisation », nous avons décrit avec précision les registres du capteur à configurer et la démarche à adopter pour mettre en œuvre le bon fonctionnement de ce capteur. La calibration est également un point très important pour obtenir des valeurs fiables. Nous avons également expliqué les étapes à effectuer pour correctement calibrer le capteur dans le document d’analyse dans la partie 6.4.3.1 et 6.4.3.2.
8.5.4. Mise en œuvre des moteurs brushless BLDC
Ce type de moteur est particulièrement intéressant dans son fonctionnement. Il permet un positionnement extrêmement précis (résolution de 0,1°) sans utiliser de codeur ou de capteur à effet hall. Ainsi, on peut effectuer un asservissement très précis avec ces moteurs avec une grande réactivité ce qui correspond parfaitement à la problématique du système. La mise en œuvre du programme a été facilitée par de nombreux exemples trouvés sur internet. De plus, l’algorithme permettant de commande ce type de moteur est relativement simple en utilisant un « lookup-table ». Cette table contient l’ensemble des trinômes de valeurs des signaux PWM à appliquer aux entrées du moteur. Ainsi, pour faire tourner le moteur, il suffit de se déplacer dans la table.
Cette technique de « Lookup table » permet d’éviter d’effectuer des calculs au niveau du microcontrôleur. Pour effectuer les premiers tests, nous avons dans un premier temps généré une
1 | Récupération des données brutes du capteur

0

2 | Application du filtre de Madgwick
3 | Conversion de la représentation quaternion en Euler
4 | Application du filtre PID
5 | Commande de la partie opérative

Figure 17 : Partie logicielle - Fonctionnement normal

19

table contenant 71 valeurs. Les moteurs utilisés possèdent 7 trinômes d’enroulements ce qui permet d’obtenir 497 pas pour 360 degrés ce qui représente une précision de 0,72 degré. Pour augmenter la précision, il suffit de générer plus de valeurs (avec une limite de 255 valeurs : résolution des PWM configurées sur 8 bits).
Pour éviter les perturbations sonores liées à la fréquence des signaux PWM, nous avons augmenté la fréquence à 18 kHz, ce qui est inaudible à l’oreille humaine. Dans certains exemples observés lors de nos recherches sur internet, la fréquence était fixée à 32 kHz. Nous avons jugé qu’une fréquence plus basse produirait le même effet en terme d’atténuation des nuisances sonores. De plus, une fréquence de fonctionnement moins élevée permet d’éviter l’échauffement des moteurs et par conséquent, la consommation énergétique du système.
8.5.5. Exploitation des données du capteur
Afin d’obtenir l’orientation du capteur dans l’espace, nous avions sélectionné la solution qui est d’utiliser l’algorithme de Madgwick. Cet algorithme, créé par un étudiant de l’université de Bristol, permet la fusion des données d’un accéléromètre, du gyroscope et d’un magnétomètre pour obtenir l’orientation sous la forme d’un quaternion. Pour effectuer l’asservissement de notre système, nous utilisons la représenter d’Euler. Une formule mathématique permet de passer d’un quaternion à Euler. Cet algorithme Open Source est utilisé dans notre programme comme une boite noire à laquelle on transmet les valeurs brutes du capteur. En retour, nous obtenons un quaternion qui peut être exploité par la suite en passant à la représentation d’Euler.
Pour plus d’informations sur l’algorithme de Madgwick : http://www.x-io.co.uk/open-source-imu-and-ahrs-algorithms/
8.5.6. Asservissement en position
L’asservissement en position est réalisé par un filtre PID. L’algorithme est implémenté sous forme de fonction et s’appuie sur les paramètres Kp, Ki, Kd propre à chaque axe. Ces paramètres sont ajustables soit dans le programme ou bien utilisant le programme de réglage. La modification de ces paramètres est décrite dans le document « Guide de l’administrateur ».
8.5.7. Architecture du programme
L’architecture du programme est décrite dans le livrable « Guide du développeur ». Pour répondre aux à la problématique d’évolutivité de la solution, nous avons construit le programme pour qu’il soit le plus paramétrable possible. Ainsi, il est possible de modifier la taille des moteurs (nombre d’enroulements) ainsi que la géométrie de la structure métallique en adaptant les paramètres. Chaque paramètre est également décrit dans le livrable « Guide l’administrateur ».
Le code source du projet est disponible en annexe du document par l’intermédiaire d’un lien Github.

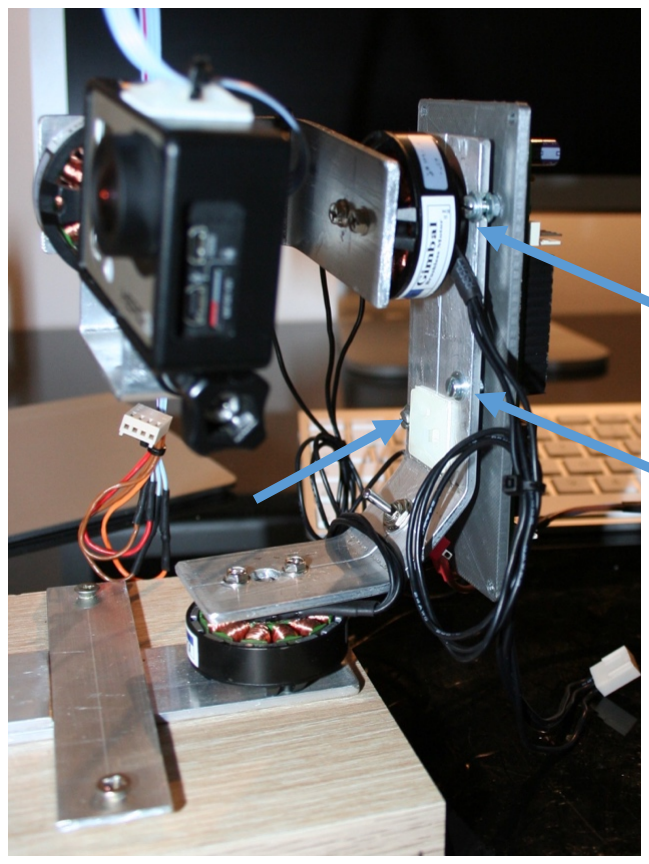
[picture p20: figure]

20

## 8.6. Intégration

La phase d’intégration a consisté à intégrer la partie électronique à la structure mécanique. L’assemblage des deux parties à été conçu par CAO afin que les points d’assemblage soient parfaitement identiques. Sur l’illustration ci-contre, on peut voir les différents points de fixations de la carte sur la structure qui correspondent aux perçages qui avaient étés prévus sur le PCB. Le fond du boitier de protection est intercalé entre la structure métallique et le PCB.
Les moteurs sont branchés sur la carte grâce à des connecteurs afin que l’ensemble soit maintenable facilement en cas de changement de moteur.
Le capteur est fixé derrière la caméra et également relié à la carte par un connecteur 4 broches pour simplifier un éventuel remplacement de la carte ou du capteur. Nous avons utilisé une nappe avec 4 fils non
torsadés | pour | éviter | les | perturbations
électromagnétiques sur le bus i2c.

Enfin, le boitier de protection est maintenu par quatre vis, facilement accessibles, toujours dans le but de faciliter la maintenance.
La batterie est maintenue sur le système via une bande de scratch, ce qui est couramment utilisé dans le domaine du modélisme pour fixer ce type de batterie. L’interrupteur de mise sous tension est fixé sur la structure métallique, au plus proche de l’arrivée de l’alimentation pour limiter la longueur de câble et l’encombrement. Pour faciliter les tests et les réglages, nous avons réalisé un support permettant de maintenir le système tel qu’illustré ci-contre.

Figure 18 : Intégration - Assemblage du prototype

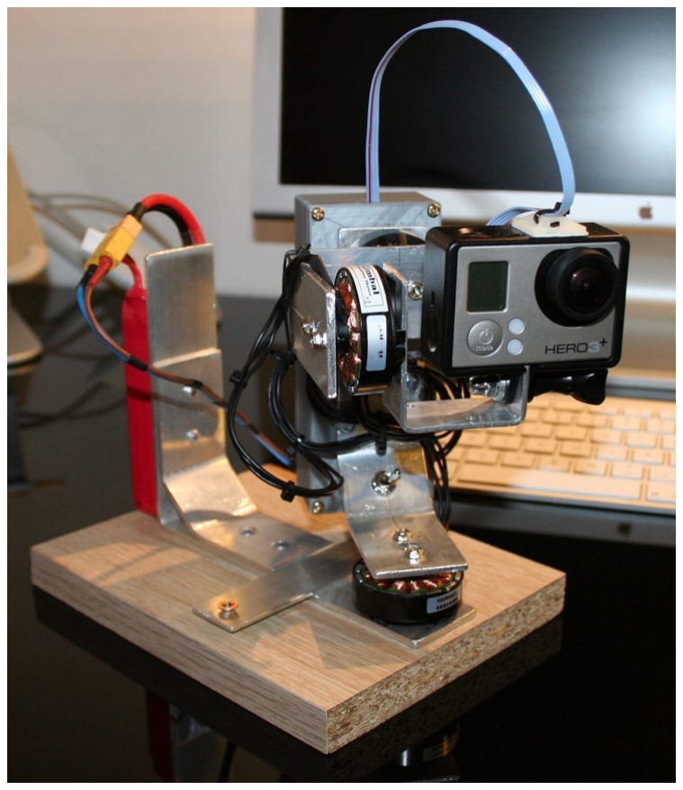
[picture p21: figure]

Figure 19 : Intégration - Assemblage du capot de protection

21

## 9. Problèmes rencontrés

- Charge de travail
Comme évoqué dans la partie « Planification », la charge de travail requise pour la réalisation de ce projet était trop importante vis-à-vis des heures allouées au PFE sur notre emploi du temps. De plus, nous avions régulièrement des créneaux de deux heures prévues sur l’emploi du temps ce qui ne permet pas de travailler efficacement sur son projet. En effet, sur des projets comme celui-ci avec une contrainte matérielle nécessite une installation et une certaine logistique qui n’est pas compatible avec un créneau de deux heures.
Si c’était à refaire, je reverrais mes ambitions à la baisse, et je proposerais un système fonctionnant sur seulement deux axes. En effet, d’un point de vue du traitement des données d’orientation, la complexité entre un traitement des données sur deux axes varie énormément.
- Complexité de l’algorithme de fusion
Malgré le fait que le prototype soit aujourd’hui fonctionnel, la partie traitement des données issues du capteur ne permet pas d’obtenir l’orientation de la caméra de façon satisfaisante. Les valeurs varient et sont instables, ce qui rend l’asservissement en position instable également.
Si c’était à refaire, je choisirais d’utiliser le DMP malgré le fait que l’on doit flasher un code binaire dont on n’a aucune idée de son fonctionnement. Cependant, cette solution permettrait au prototype de fonctionner parfaitement et d’obtenir une stabilisation idéale grâce à des données fiables.
- Perturbations électromagnétiques
Lors des tests effectués sur la carte électronique, nous avons testé l’ensemble des fonctions de façon unitaire. Chaque test a été effectué avec succès. Néanmoins, nous nous sommes aperçus d’un dysfonctionnement lorsque nous faisions l’acquisition des données du capteur en même temps de la commande des moteurs. Ce dysfonctionnement était dû à des perturbations électromagnétiques induites par la commande des moteurs. En effet, nous utilisons trois signaux PWM pour la commande d’un moteur. Ayant sur la carte trois moteurs, cela fait au total neuf signaux PWM à une fréquence de 18 kHz qui émettent en même temps. Cela avait pour conséquence de perturber le bus i2c, ce qui rendait la communication avec le capteur impossible.
Pour résoudre ce problème, nous avons effectué des tests à l’aide d’un oscilloscope pour observer les trames sur le bus i2c. Ces observations n’ont révélé rien de probant. Nous avons fait l’hypothèse que des pics de courant pouvaient perturber le bus. Nous avons effectué des tests en ajoutant des résistances en série sur le bus et avons constaté une amélioration permettant de faire fonctionner l’acquisition des données en même temps que la communication.

## 10. État d’avancement du projet

Le projet s’est réalisé sur une durée de 5 mois et a abouti à un prototype fonctionnel. Cependant, comme expliqué dans la partie « Problèmes rencontrés », la fonction de traitement des données ne permet pas d’obtenir des résultats satisfaisants.
Le système répond aux spécifications établies en début de projet et peut aboutir rapidement à un prototype pleinement fonctionnel en terme de stabilisation de caméra. En effet, seule la fonction de traitement des données est à revoir. Nous avons pu tester l’ensemble des fonctions au cours du développement et avons validé le fonctionnement de chacune.
Il reste cependant une fonction à implémenter qui est la correction de l’orientation de la caméra en fonction des mouvements de l’utilisateur (fonction décrite dans le cahier de spécification dans la partie 4.2). Cette fonction est purement algorithmique et ne nécessite pas de connaissances particulières.

22

Une vidéo de démonstration du prototype est disponible à l’adresse suivante : https://www.youtube.com/watch?v=LZprc0sueDk

## 11. Perspectives d’évolution

Étant à l’initiative de ce projet, je souhaite continuer son développement et résoudre le problème de traitement des données évoqué dans la partie « Problèmes rencontrés ».
Afin d’alléger le système, je prévois de remplacer certaines bielles actuellement en aluminium par des pièces en PLA imprimée en 3D. Cela permettrait de rendre le système plus maniable et moins consommateur en énergie.
Il peut également être étudié d’ajout d’une connectivité Bluetooth pour permettre d’effectuer les réglages du système depuis une application Smartphone et de pouvoir ajouter plusieurs modes de fonctionnement.

## 12. Conclusion

Ce projet est à mon sens un aboutissement dans ma formation d’ingénieur. Cela m’aura permis de mettre en œuvre un grand nombre de compétences techniques, mais surtout organisationnelles. Tout au long du projet, j’ai travaillé à prendre du recul sur les choix que j’ai effectués. Cette démarche m’a permis de mener à bien ce projet d’envergure, dans lequel je me suis beaucoup investi et qui m’a passionné.

## 13. Annexes

## Ressources

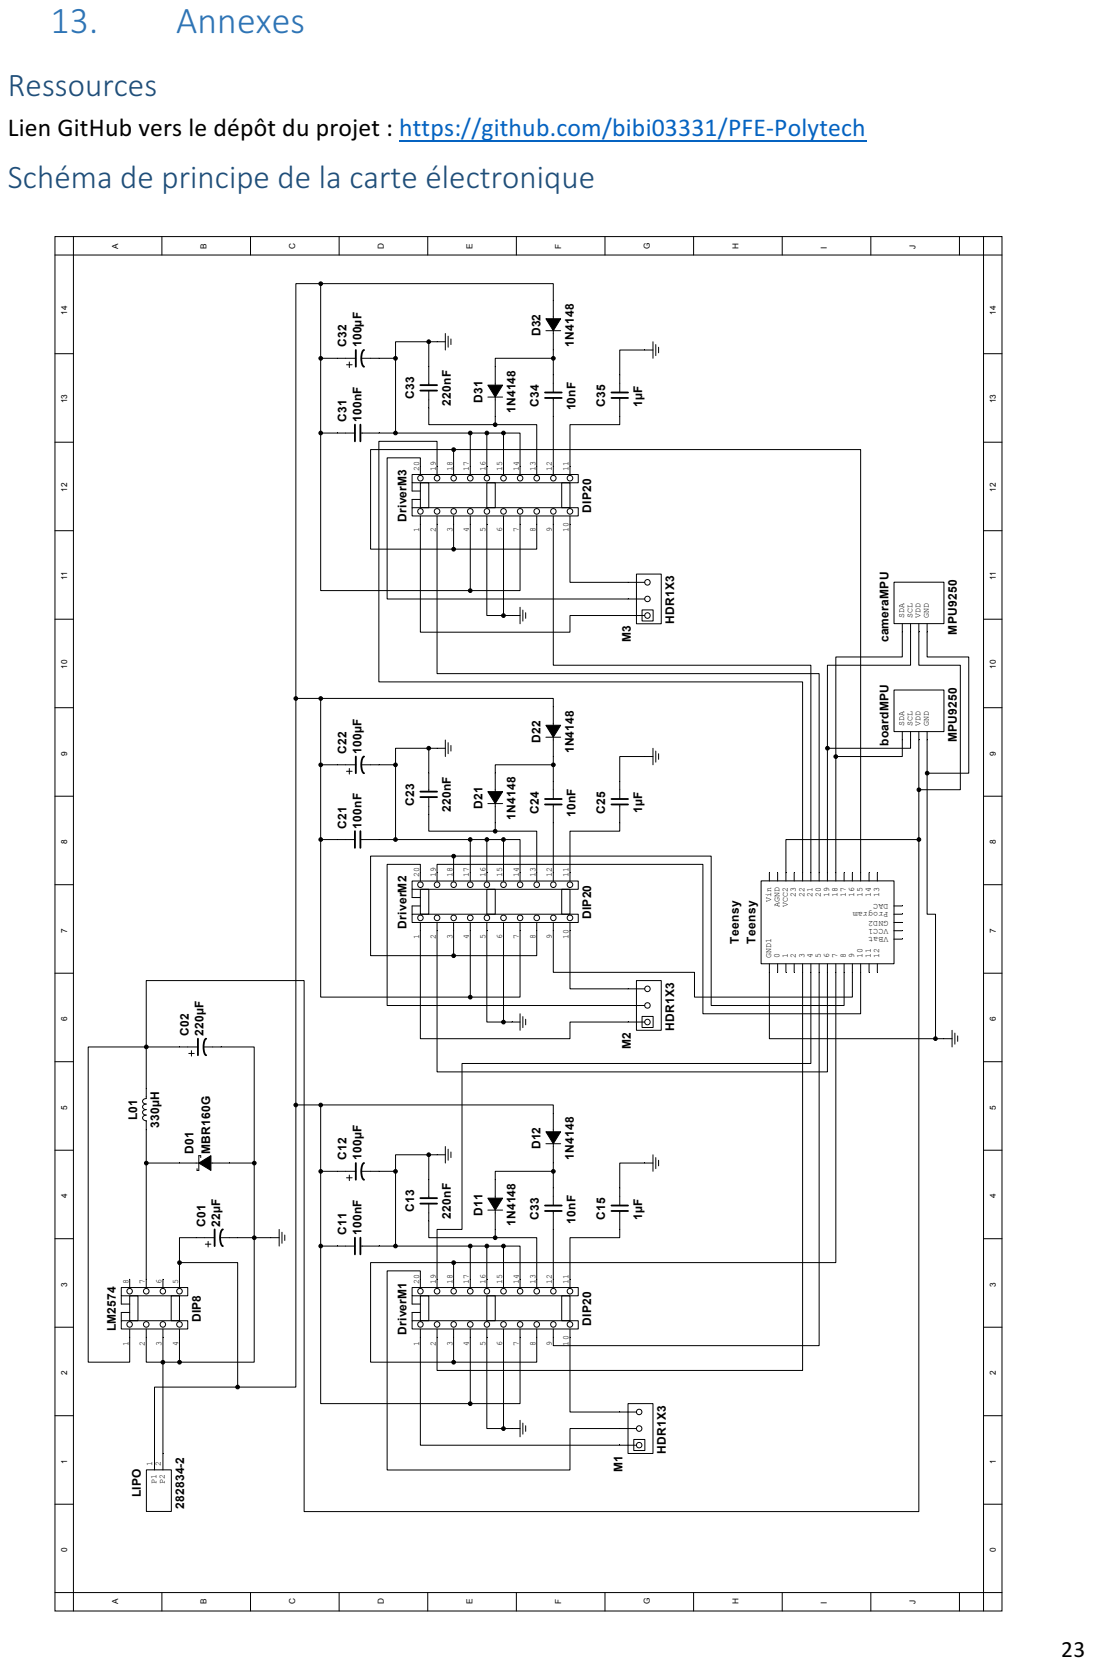
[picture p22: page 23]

Lien GitHub vers le dépôt du projet : https://github.com/bibi03331/PFE-Polytech
Schéma de principe de la carte électronique

24

## 14. Table des figures

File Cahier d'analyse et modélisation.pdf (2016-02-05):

1

## École Polytechnique de l’Université de Tours

64, Avenue Jean Portalis
37200 TOURS, France
Tél. +33 (0)2 47 36 14 14

## www.polytech.univ-tours.fr

# Département Informatique industrielle

# Analyse et modélisation

Projet : | Système de stabilisation motorisé pour caméra
Réalisé par : | Sébastien LAPORTE | Encadré par : | Ameur SOUKHAL
Début du projet : | 22/09/2015 | Fin du projet : | 10/02/2015

Historique des modifications

Version | Date | Note de version
1.0 | 04/01/2016 | Version de dépôt initial

2

## Table des matières

3

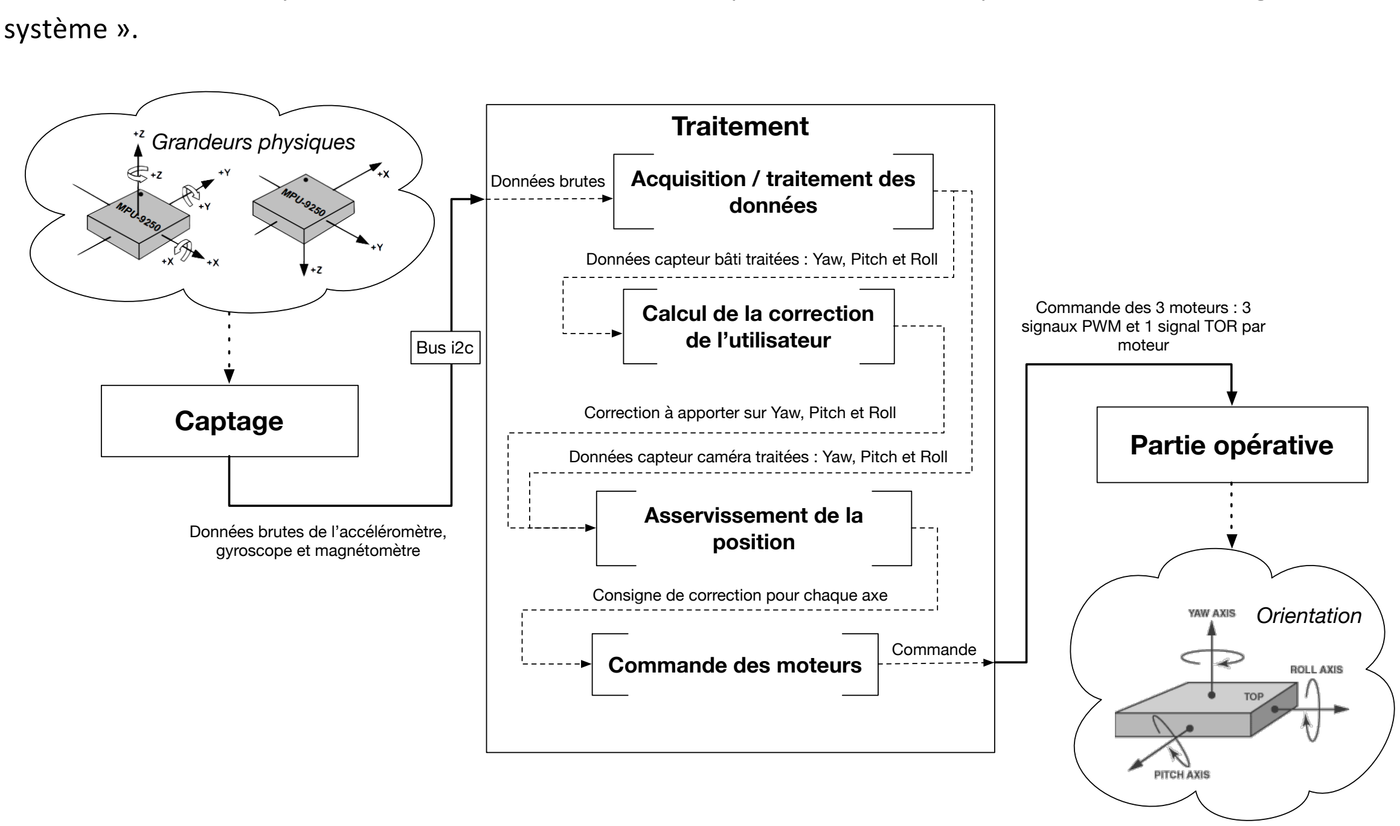
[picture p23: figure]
système ».; Captage; Traitement; Acquisition / traitement des données; Asservissement de la position; Commande des moteurs; Partie opérative; Grandeurs physiques; Bus i2c; Données brutes de l’accéléromètre, gyroscope et magnétomètre; Consigne de correction pour chaque axe; Données brutes; Commande; Commande des 3 moteurs : 3 signaux PWM et 1 signal TOR par moteur; Orientation; Calcul de la correction de l’utilisateur

4

## 1. Introduction

Ce document a pour objectif d’expliquer en détail les choix et solutions mises en place pour la réalisation du projet de fin d’étude. Ce rapport est organisé en plusieurs sous-parties : Électronique, mécanique et logicielle. En effet, comme défini dans le cahier de spécifications, l’objectif de ce projet est de réaliser un prototype abouti d’un système de stabilisation d’une caméra d’action sur trois axes. Le porteur du projet qui agit également en tant que MOE est Sébastien Laporte, étudiant en cinquième année de cycle d’ingénieur en informatique industrielle. L’encadrant du projet représentant la MOA est Monsieur Ameur Soukhal, enseignant chercheur au CNRS.

## 2. Contexte et objectif du projet

Depuis quelques années, le marché des caméras d’action est en constante évolution. C’est la marque GoPro qui a démocratisé ce type de matériel et qui s’est imposée comme leader dans le domaine. Grâce à cette gamme de caméra, il est possible de filmer ses activités sportives, sur tous les terrains avec un minimum d’encombrement. Cependant, malgré la miniaturisation et la qualité du capteur, il est souvent difficile de filmer de manière stable lorsqu’on conduit une moto ou que l’on descend une piste de ski. L’objectif de ce projet est de concevoir et réaliser un système de stabilisation pour caméra d’action. Fixée sur le système, la caméra sera stabilisée de façon mécanique pour permettre à l’utilisateur de filmer tout en conservant une image stable. De nombreuses solutions existent aujourd’hui. Pour ce projet, nous avons la volonté de développer notre propre solution pour appréhender l’ensemble des problématiques et technologies.

## 3. Architecture générale du système

Le schéma ci-dessous présente l’architecture du système, il est issu du cahier de spécifications. Chaque élément est traité dans les différentes partie : électronique, mécanique et logicielle. Pour plus de précisions sur le fonctionnement du système, se référer au cahier de spécification au chapitre « Architecture générale du

Figure 1 : Architecture générale du système

Données capteur caméra traitées : Yaw, Pitch et Roll

Données capteur bâti traitées : Yaw, Pitch et Roll

Correction à apporter sur Yaw, Pitch et Roll

5

## 4. Partie électronique

Dans cette première partie, nous allons présenter l’ensemble des composants qui ont été choisi pour la partie électronique et la manière dont nous avons architecturé les fonctions électroniques.

## 4.1. Choix des technologies

Le choix des technologies a été réalisé suite à la phase de rechercher et de spécifications. L’ensemble des références sélectionnées se trouvent en annexe. Le prix des composants se trouvent sur les factures également en annexe.

Remarque : L’ensemble du matériel sélectionné est très spécifique à ce domaine d’application. En effet, lors de la phase de recherche, nous nous sommes intéressé au domaine des drones, notamment aux systèmes de stabilisation de caméra appelés « nacelles ». Ces technologies étant très spécifiques, la majorité des composants n’a donc pas nécessité d’étude comparative tant le nombre de référence de produit est restreint.

### 4.1.1. Capteur

Au cours de l’étude qui a été menée pour le choix du capteur, nous avons sélectionné deux modèles pour la réalisation des prototype 2 axes et 3 axes. En effet, dans un premier temps, nous avons réalisé un prototype sur 2 axes dans le but d’appréhender les notions inhérentes à cette technologie de capteur. Puis, pour répondre au cahier et des charges, nous avons dû reprendre une phase d’étude pour choisir un nouveau capteur pour modéliser les mouvements sur 3 axes d’une façon optimale.

Remarque : Ce choix technologique est étroitement lié avec l’étude qui a été menée sur l’exploitation des données.

Pour modéliser l’orientation d’un solide dans l’espace, il existe 4 grandes familles de capteur :

- Gyroscope : Capteur permettant de mesurer la vitesse angulaire. L’unité de mesure est le degré / seconde ou encore le radian / seconde.
- Accéléromètre : Capteur permettant de mesurer l’accélération linéaire sur les axes X, Y et Z. L’unité de mesure est le m/s$ ou peut également être exprimé en « g ».
- Magnétomètre : Également appelé boussole, ce capteur permet de mesurer le champ magnétique de l’environnement. L’unité de mesure est le Tesla ou le Gauss.
- Altimètre : Un altimètre permet de mesurer une distance verticale entre un point et une surface de référence un mesurant un niveau de pression atmosphérique.
4.1.1.1. Capteur pour un prototype sur deux axes

Pour modéliser l’orientation d’un solide sur les deux axes : Pitch et Roll, il est nécessaire d’utiliser un gyroscope et un accéléromètre. En effet, nous verrons dans la partie « Exploitation des données » que l’utilisation de ces deux types de capteurs permet d’obtenir les données souhaitées.

6

Nous avons sélectionné le capteur MPU-6050 de la société InvenSens qui est une référence incontournable dans ce domaine. Ce capteur a l’avantage de proposer dans un même composant un accéléromètre et un gyroscope ce qui élimine les problèmes d’alignement. La communication avec ce capteur s’effectue en i2c. La précision et la sensibilité de ce capteur est paramétrable : ±250, ±500, ±1000, and ±2000 °/sec pour le gyroscope et ±2g, ±4g, ±8g, and ±16g pour l’accéléromètre ce qui permet d’avoir un champs d’application extrêmement large. Dans le cadre de ce projet, les sensibilités minimales seront suffisantes.

Ce capteur étant uniquement produit en CMS, nous avons sélectionné un
fabriquant proposant ce capteur sur un PCB avec les composants nécessaires à
son fonctionnement : Le capteur IMU 6 DoF MPU-6050 par Drotek. La carte peut être alimentée en 5 ou 3,3v.
4.1.1.2. Capteur pour un prototype sur trois axes

L’ajout de l’axe Yaw pour la modélisation sur trois axes ajoute une complexité technique. Au cours de mes recherches, j’ai pu rencontrer plusieurs solutions permettant d’obtenir l’orientation les 3 axes. Dans certains cas, l’orientation est obtenue uniquement grâce à un accéléromètre et un gyroscope. Cependant cette solution n’est pas optimale. En effet, un gyroscope « drift » au cours du temps, ce qui donne une orientation erronée sur l’axe Yaw. Pour compenser ce glissement, il est possible d’ajouter un autre
capteur : un magnétomètre. Cette solution sera plus détaillée dans la
partie « Exploitation des données ».

La société InvenSens propose également un capteur doté d’un gyroscope, d’un accéléromètre et d’un magnétomètre dans un même composant : Le MPU-9250. Là encore, l’entreprise Drotek propose ce capteur sur un PCB intégrant les composants électroniques nécessaires à son fonctionnement. La carte peut être alimentée en 5 ou 3,3v.

### 4.1.2. Motorisation

4.1.2.1. Les moteurs

La motorisation est un élément essentiel du système car ce sont les moteurs qui vont être garant de la stabilisation de la caméra. Il existe aujourd’hui sur le marché une très large gamme de moteurs. Lors de la phase de recherche, nous avons constaté qu’il existe deux types de moteurs utilisés pour ce type d’application : Les servomoteurs et les moteurs brushless. Les servomoteurs on l’avantage d’être relativement simple à commander. De plus, de nombreuses librairies permettent de faciliter leur commande. L’inconvénient est qu’ils sont peu précis : de l’ordre 1°. C’est à cause de cette précision insuffisante que nous avons décidé de ne pas utiliser de type de moteur.

Les moteurs brushless sont usuellement couplés à un capteur à effet hall pour connaître la position de celui-ci et effectuer l’asservissement. Lors de nos recherches, nous avons découvert un nouveau type de moteur qui est largement utilisé aujourd’hui pour motoriser les nacelles de drones. Ces moteurs sont dits BLDC pour Brushless DC. Ce type de moteur est commandé par 3 signaux PWM comme le montre la figure ci-dessous.

Figure 2 : MPU-6050 par Drotek

Figure 3 : MPU-9250 par Drotek

7

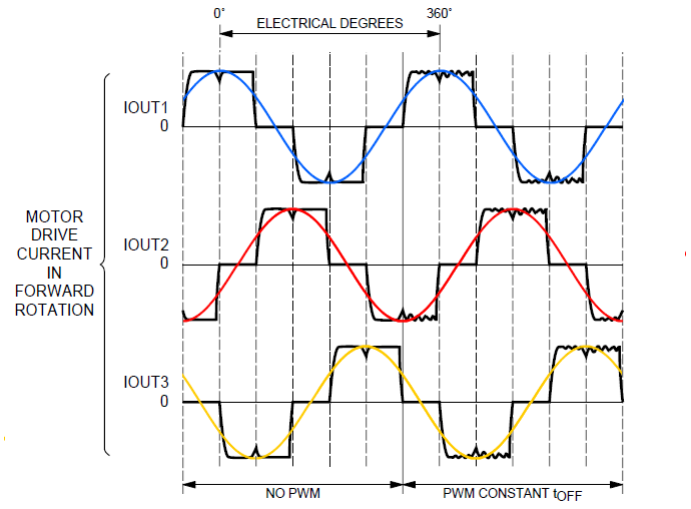
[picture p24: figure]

Figure 4 : Signaux de commande d'un moteur BLDC On peut observer sur la figure ci-dessus qu’il est possible d’obtenir une position en degrés à partir d’un trinôme de signaux PWM. Lors de tests sur un banc d’essaie, nous avons pu constater une précision de 0,1° ce qui est tout à fait satisfaisant pour notre système.

Pour trouver une référence de ce type de moteur, nous nous sommes
orientés vers une boutique spécialisée dans les pièces détachées pour
drones. Le choix s’est porté sur une référence d’entrée de gamme car elle correspond à notre besoin. En effet, le type de camera que nous souhaitons stabiliser est relativement légère (environ 110g). Nous avons choisi la référence GBM3508-130 qui permet de stabiliser des caméras dans une gamme de poids allant de 200 à 400g, ce qui est largement en dessous de notre spécification. Néanmoins, cette sécurité est justifiée par le poids non négligeable de la structure à réaliser, qui peut être plus important que celui des structures du commerce (habituellement en plastique ou en carbone).
4.1.2.1. Les drivers de moteur

La technologie de ces moteurs BLDC implique l’utilisation d’un driver spécifique. STmicroelectronics commercialise un driver pour ce type de moteur : Le L6234 est un contient trois ponts en H et permet de commander en puissance les moteur brushless DC. Ce composant existe au format DIP20 et en CMS. Il permet de commander les moteurs jusqu’à une fréquence de 50 KHz ce qui correspond au besoin. La plage d’alimentation du moteur peut varier entre 7 et 52v avec un courant maximum de 5A. La tension d’alimentation recommandée pour les moteurs sélectionnés est entre 7 et 12v ce qui correspond à la plage de fonctionnement. Le courant maximum de 5A ne sera jamais atteint avec le poids de la caméra utilisé.

Figure 6 : L6234 par Drotek

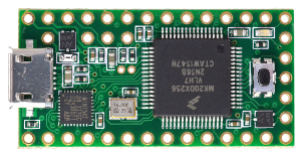
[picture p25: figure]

8

Afin de réaliser des tests sur un banc d’essai, nous avons fait le choix dans un premier temps d’utiliser une platine de développement intégrant un driver L6234 avec l’électronique nécessaire à son fonctionnement. Cette Breakout Board est conçue par la société Drotek. La conception électronique qu’ils ont réalisé s’appui sur une note d’application fournie par ST.

### 4.1.3. Microcontrôleur

L’élément central du système doit permettre d’effectuer l’acquisition des données par le biais d’un bus i2c et de pouvoir commander les trois moteurs. Nous verrons dans la partie « Exploitation des données » que le traitement requiert une grande capacité de calcul. La commande des trois moteurs implique 9 sorties permettant de produite un signal PWM ainsi que 3 sorties TOR. De plus, il est nécessaire de faire fonctionner ces PWM à une fréquence de 32 Khz.

Dans un premier temps, nous avons étudié l’ensemble des solutions qui étaient à notre disposition. L’utilisation d’un PIC a rapidement été éliminée. En effet, ce type de microcontrôleur ne dispose du nombre de sorties PWM requis pour le système. De plus, la fréquence de fonctionnement n’est pas suffisante. Nous avons envisagé la solution du co-design avec l’utilisation d’un FPGA. Cependant, cette solution n’aurait pas permis d’aboutir à un prototype suffisamment compact et transportable à cause de l’utilisation d’une plateforme de développement. Pour finir, nous avons recherché un microcontrôleur sur base ARM. Ce type de matériel dispose d’un grand nombre d’entrées / sorties et peut fonctionner à des fréquences intéressantes pour notre système. Nos recherches nous ont mené à la carte Teensy 3.1.

La Teensy est une plateforme de développement extrêmement
compacte, animée par un microcontrôleur ARM Cortex M4 qui peut
fonctionner à 96Mhz et qui dispose de 12 sorties capable de produire un signal PWM. Cette carte peut être alimentée en 5v ou en 3,3v. Ses dimensions sont : 35 mm x 18 mm.

### 4.1.4. Alimentation

Le système possède deux besoins en alimentation : Une alimentation très basse tension pour l’alimentation des éléments de commande (Capteur, microcontrôleur) et une alimentation dite de puissance pour les moteurs (par l’intermédiaire des drivers). Comme indiqué dans le cahier des charges, le système doit être autonome en énergie.

4.1.4.1. Choix de la batterie

Les moteurs sélectionnés peuvent consommer au maximum jusqu’à 5A chacun. Avec 3 moteurs, il est donc nécessaire d’avoir une batterie qui puisse fournir un courant maximum de 15A environ. Pour répondre à ce besoin, la technologie LIPO est tout à fait appropriée. Ce genre de batterie est utilisée pour motoriser des drones. Ayant besoin d’une tension comprise entre 7 et 12v, nous avons choisi d’utiliser une batterie LIPO 3S (qui signifie que la batterie possède 3 éléments). La tension de cette batterie est de 11,7v. Nous avons choisi dans un premier temps d’utiliser une batterie de 2200 mAh. Cette valeur pourrait être ajustée lors de tests afin de correspondre à une autonomie d’1 heure qui est spécifiée dans le cahier des charges. La batterie sélectionnée possède un courant maximum de 70A, ce qui est largement suffisant pour notre besoin.

4.1.4.2. Régulation de l’alimentation en 3,3v

L’alimentation des capteurs et du microcontrôleur peut être faite en 5 ou 3,3v. Concevant un système qui doit être autonome, nous souhaitons réduire au maximum la consommation. Pour cela, nous choisissons d’alimenter ces éléments en 3,3v. Pour réaliser cette fonction, nous avons décidé de réaliser une alimentation à découpage.

Figure 7 : Teensy 3.1

9

En effet, cette solution est la plus appropriée pour ce type d’application car il est moins consommateur d’énergie qu’une simple alimentation basée sur un régulateur de tension. De plus, cette solution peut être simplement mise en place par l’utilisation d’un composant tel que le LM2574. Celui-ci permet de réguler une tension d’entrée avec une tension maximale de 40v ce qui est bien au dessus de a tension de la batterie sélectionnée. Ce composant est disponible au format DIP-8.

## 4.2. Schémas fonctionnels

Les schémas fonctionnels ont pour objectif de définir l’ensemble des fonctions électroniques du système. Pour chaque sous-ensemble, nous avons identifié les signaux en entré et en sortie.

Remarque : L’alimentation n’est pas mentionnée dans l’ensemble des blocs.

### 4.2.1. Fonction « Alimentation »

La fonction d’alimentation permet de fournir une tension régulée de 3,3v à partir de la batterie. Cette fonction permettra d’alimenter le microcontrôleur ainsi que le capteur.

Figure 8 : Partie électronique - Schémas fonctionnels - Fonction alimentation

### 4.2.2. Fonction « Traitement des données »

Le traitement des données est assuré par le microcontrôleur. Ce bloc fonction permet d’identifier l’ensemble des signaux. En entré nous avons SDA et SCL qui correspondent au bus i2c, pour la communication avec le capteur. En sortie, ce sont les signaux qui permettent de commander les moteurs par l’intermédiaire des driver de moteur.

Figure 9 : Partie électronique - Schémas fonctionnels - Fonction traitement des données

Alimentation

vBat 11,7v | vReg 3,3v

Traitement

IN1_MOT1
IN2_MOT1
IN3_MOT1

IN1_MOT2
IN2_MOT2
IN3_MOT2

IN1_MOT3
IN2_MOT3
IN3_MOT3

EN_MOT1

EN_MOT2

EN_MOT3

SDA
SCL

10

### 4.2.3. Fonction « Captage »

La fonction captage permet de récupérer les informations d’orientation. Cette fonction est assurée par le capteur i2c.

Figure 10 : Partie électronique - Schémas fonctionnels - Fonction captage

### 4.2.4. Fonction « Commande moteur »

Pour commander en puissance les moteurs, nous utilisons le driver de moteur L6234. C’est ce composant qui remplit la fonction « Commande moteur » en fonction des signaux issus du microcontrôleur. En sortie de ce bloc fonction, ce sont les trois phases du moteur.

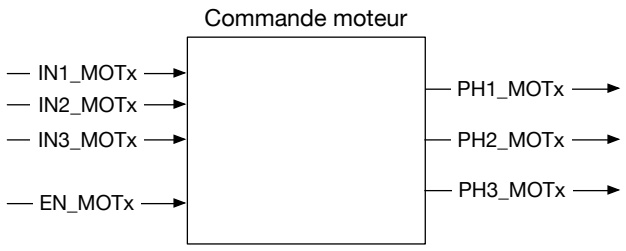
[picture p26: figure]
Commande moteur; IN1_MOTx IN2_MOTx IN3_MOTx; EN_MOTx; PH1_MOTx; PH2_MOTx; PH3_MOTx

Figure 11 : Partie électronique - Schémas fonctionnels - Fonction commande moteur

### 4.2.5. Schéma fonctionnel du système

Sur le schéma fonctionnel ci-dessous, on retrouve l’ensemble des fonctions précédemment présentées.

Figure 12 : Partie électronique - Schéma fonctionnel du système

Captage

SDA
SCL

11

En terme d’alimentation, les blocs fonction « Captage » et « Traitement » sont alimentés en 3,3v par le bloc fonction « Alimentation ». Les trois blocs fonction de « Commande moteur » sont eux directement alimentés par la batterie.

12

## 5. Partie mécanique

Ce nouveau chapitre est dédié à la modélisation et à la conception mécanique du système. L’objectif de la partie mécanique du système est d’assurer le maintient de la caméra sur trois articulations effectuées par les moteurs. Cette partie comprend également la modélisation des éléments de protection des cartes électronique.

## 5.1. Schéma du système

Le schéma ci-dessous défini le repère du système et les noms associés aux moteurs, il est issu du cahier de spécifications. Lors de la phase de spécifications, nous avions spécifié l’utilisation de deux capteurs : un sur le bâti et un sur la caméra. Lors de la phase d’analyse, nous nous sommes aperçu que le capteur du bâti n’est pas nécessaire pour assurer le fonctionnement du système tel qu’il est spécifié. Cette explication sera détaillée dans la partie logicielle avec la modélisation de la fonction « Correction de l’orientation ».


Figure 13 : Schéma général du système La schématisation de la structure mécanique est nécessaire avant d’effectuer la modélisation du système par un logiciel de DAO. Dans un premier temps, nous avons entrepris des recherches pour observer les différentes structures réalisées sur des systèmes similaires. Cette conception doit également prendre en compte le type de matériaux à utiliser. En effet, dans le cadre de ce projet, le prototype doit être réalisable par nous même afin de limiter le coût de fabrication. Cependant, la réalisation doit pouvoir être sous traitée si l’on souhaite effectuer la production d’une petite série du système.


13

## 5.2. Modélisation de la structure

Une première modélisation de la partie mécanique sous formes de schémas permet de définir la structure de base du système. Ces schémas seront le point de départ de la CAO. Ils définissent également le nom de pièces maitresses de la structure.

### 5.2.1. Schémas complets

Le schéma ci-dessous représente le système en vue de côté. La structure est constituée de 3 articulations : Une pour chaque axe. Les bielles sont identifiées par le nom de l’axe d’articulation.

La bielle Pitch supporte le support de caméra. Celui-ci sera fixé par vis et écrous à main pour pouvoir être démonté rapidement par l’utilisateur. Le capteur est également lié à cette bielle pour estimer l’orientation de la caméra.

La carte électronique sera fixée sur la bielle Yaw car cet emplacement permet de limiter les torsions sur les câbles des moteurs. En effet, les deux moteurs liés à cette bielle (Moteur Roll et moteur Yaw) sont fixés par leur stator ce qui permet de les relier électriquement à la carte électronique sans avoir d’articulation entre les câbles.

Le bâti permet de fixer la batterie. C’est aussi cette partie qui permet à l’utilisateur de porter le système. En effet, grâce à l’épaisseur de la batterie, celle-ci constitue une véritable poignée pour l’utilisateur.

Figure 14 : Schéma structure mécanique - Vue de coté


14

Le schéma ci-après présente le système en vue de face. On retrouve les différents éléments présentés précédemment. L’objectif est d’obtenir un équilibre mécanique lorsque la caméra est installée pour limiter les efforts des moteurs. Cette contrainte est à prendre en compte pour la CAO.

Figure 15 : Schéma structure mécanique - Vue de face

15

### 5.2.2. Schémas des pièces

Bielle Yaw | Bâti / Support


Figure 16 : Modélisation mécanique - Bielle Yaw | Figure 17 : Modélisation mécanique - Bâti / Support
Bielle Pitch | Bielle Roll


Figure 18 : Modélisation mécanique - Bielle Pitch | Figure 19 : Modélisation mécanique - Bielle Roll

## 5.3. Conception des éléments de la structure

Bielle Yaw; Bielle Roll; Bielle Pitch; Bâti et renfort

Nous avons utilisé le logiciel SolidWorks pour modéliser et dimensionner les pièces précédemment présentées.
Cette conception permet de produire des plans de chaque pièce pour la réalisation.

Remarque : L’ensemble des plans et fichiers 3D se trouvent en annexe de ce document.

Figure 21 : CAO - Bielle Roll 3D

Figure 20 : CAO - Bielle Yaw 3D

Figure 22 : CAO - Bielle Pitch 3D

Figure 23 : CAO - Bâti et renfort 3D

17

## 5.4. Conception des éléments de protection

Afin de protéger la carte électronique et le capteur, nous avons conçu deux boitiers de protection toujours avec le logiciel SolidWorks. L’objectif est de réaliser ces pièces par impression 3D. Lors de la conception, nous avons donc pris en compte les contraintes liées à ce genre de réalisation : éviter les angles vifs, épaisseur minimum des parois de 3mm.

Remarque : Un lien vers les fichiers STL est en annexe.

Boitier carte électronique
(Dessus)

Boitier carte électronique
(Dessous) | Couvercle carte électronique


Boitier capteur IMU | Couvercle capteur

18

## 5.5. Choix techniques pour la réalisation

### 5.5.1. Matériaux utilisés pour la structure

La fabrication du prototype doit être réalisable avec les équipements de l’école. En effet, afin de limiter le coût du projet la réalisation sera effectuée par nos soins. Pour réaliser les pièces précédemment présentées, nous avons choisi d’utiliser des profilés en aluminium. Ce matériau est léger et peut être plié sans machine spéciale. L’épaisseur et les dimensions des profilés seront à déterminer au cours de la CAO, en prenant en compte les paramètres de résistance (poids de la caméra et des moteurs) et d’encombrement.

### 5.5.2. Technique de réalisation des éléments de protection

Pour la réalisation des boitiers, il a été fait le choix d’utiliser l’impression 3D. En effet, ce type de pièce se prête très bien à ce type de réalisation car cela permet d’obtenir une pièce relativement complexe avec un très faible coût.

### 4.4.2. Fixation de la caméra

Pour fixer la caméra sur le système, nous avons choisi d’utiliser un boitier GoPro type « Frame » comme illustré ci-dessous pour maintenir efficacement la caméra. La bielle Pitch est pourvue d’un trou de fixation pour l’assemblage. Cette solution permet également de s’adapter à plusieurs caméras de la marque GoPro.


Figure 24 : Partie mécanique - Fixation caméra

19

## 6. Partie logicielle

Cette partie présente l’ensemble des techniques et méthode utilisées pour remplir les fonctions du système. Ce chapitre présente les différentes méthodes envisagées et mises en place pour un prototype sur deux axes puis un prototype final sur trois axes.

Les deux techniques d’exploitation des données ont été mises en place sur un prototype. L’ensemble des techniques qui ont permis d’aboutir au choix de la solution ont également été testé et implémenté.

## 6.1. Exploitation des données d’un capteur IMU 6 DoF

Dans la phase de recherche de solution, nous avons dans un premier temps entrepris des tests avec un capteur IMU 6 DoF : le MPU-6050. Afin d’appréhender cette technologie, nous nous sommes limités à faire l’acquisition des données sur deux axes : Pitch et Roll.

Pour rappel, le capteur MPU-6050 possède deux type de capteur : un gyroscope et un accéléromètre. Pour obtenir l’orientation du capteur avec Pitch et Roll il est nécessaire d’effectuer un traitement sur les données brutes issues des capteurs. Pour cela, nous avons essayé deux méthodes : Le filtre le Kalman et le filtre complémentaire.

Le filtre de Kalman est un outil complexe à utiliser. Tout comme l’autre filtre que nous avons utilisé, il permet d’obtenir une estimation de l’orientation du capteur à partir des données d’un accéléromètre et d’un gyroscope. Les résultats obtenus avec ce filtre sont tout à fait satisfaisant. Cependant l’implémentation d’un tel filtre n’est vraiment pas aisé et l’ajustement des paramètres de celui-ci requiert un travail non négligeable pour arriver à une estimation correcte. Dans un second temps, nous sous sommes intéressé au filtre complémentaire qui est décrit dans la littérature comme beaucoup plus simple que celui de Kalman.

Le filtre complémentaire est relativement simple à mettre en place. En effet, le calcul de ce filtre tient en une seule ligne de calcul. De plus, l’ajustement des paramètres est assez rapide à effectuer. Ci-dessous, voici l’algorithme permettant de faire une estimation de l’orientation sur les deux axes : Pitch et Roll.

Dans un premier temps il est nécessaire d’appliquer une formule mathématique permettant d’obtenir Roll et Pitch. Ces valeurs sont non filtrées et ne sont pas exploitable :

roll = atan2(accY, accZ) ∗ RAD_TO_DEG;

pitcℎ = atan(−accX / sqrt(accY ∗ accY + accZ ∗ accZ)) ∗ RAD_TO_DEG;

Figure 25 : Équations roll et pitch
Pour obtenir l’estimation de l’orientation, on applique le filtre complémentaire qui est de la forme suivante :

compAngleX = 0.96 ∗ (compAngleX + gyroXrate ∗ dt) + 0.04 ∗ roll;

compAngleY = 0.97 ∗ (compAngleY + gyroYrate ∗ dt) + 0.03 ∗ pitcℎ;

Figure 26 : Équations filtre complémentaire Les variables gyroXrate et gyroYrate correspondent au données brutes du gyroscope en degrés par seconde. Les variables numériques correspondent au paramètres du filtre. L’addition de ces deux paramètres doit obligatoirement être égal à 1.

20

Au cours des tests, nous nous sommes aperçu que les résultats obtenus avec un filtre complémentaire sont presque identiques à ceux obtenus avec un filtre de Kalman. En conclusion, pour estimer l’orientation d’un solide sur les deux axes Pitch et Roll, la solution retenue est le filtre complémentaire.

Remarque : Les codes utilisés pour l’implémentation d’un filtre de Kalman et d’un filtre complémentaire sont disponibles en annexe de ce document.

## 6.2. Exploitation des données d’un capteur IMU 9 DoF

Dans la précédente partie, nous avons traité l’exploitation des données issues d’un capteur 6 axes pour modéliser l’orientation d’un solide sur deux axes. Cependant, l’utilisation d’un tel capteur pour modéliser l’orientation sur trois axes est problématique. En effet, l’ajout de l’axe Yaw complexifie le problème. Pour effectuer l’acquisition des données sur 3 axes, l’utilisation d’un simple filtre complémentaire ne suffit plus. C’est pour cela que nous avons essayé un autre capteur : le MPU-9250. Celui-ci intègre un magnétomètre en plus d’un accéléromètre et gyroscope.

Pour obtenir l’orientation du capteur sur les trois axes à partir des données des trois capteurs nous avons utilisé un algorithme de fusion nommé « Algorithme de Madgwick ». Sébastien Madgwick est un ancien étudiant de l’université de Bristol qui a mis au point un algorithme permettant de faire l’estimation de l’orientation d’un objet en 3D. Dans son rapport figure l’implémentation en langage C de son algorithme. Nous avons utilisé cet algorithme comme une boite noire pour exploiter le capteur MPU-9250 et ainsi obtenir l’orientation sur Yaw, Pitch et Roll. En effet, ses travaux s’appuient sur les quaternions, un outil mathématique que nous ne maitrisons pas. Ci-dessous, le diagramme représentant le filtre mis en place, prenant en compte les données d’un gyroscope, accéléromètre et d’un magnétomètre.


Figure 27 : Diagramme du filtre de Madgwick Le magnétomètre permet de compenser le glissement naturel du gyroscope. En sortie du filtre, on obtient le résultat de l’orientation sous la forme d’un quaternion. Les formules suivantes permettent d’obtenir les composantes Yaw, Pitch et Roll à partir des quaternions.


21

yaw = atan2(2.0f ∗ (q[1] ∗ q[2] + q[0] ∗ q[3]), q[0] ∗ q[0] + q[1] ∗ q[1] − q[2] ∗ q[2] − q[3] ∗ q[3])

pitcℎ = −asin(2.0f ∗ (q[1] ∗ q[3] − q[0] ∗ q[2]))

roll = atan2(2.0f ∗ (q[0] ∗ q[1] + q[2] ∗ q[3]), q[0] ∗ q[0] − q[1] ∗ q[1] − q[2] ∗ q[2] + q[3] ∗ q[3])

Figure 28 : Yaw Pitch Roll à partir des quaternions

## 6.3. Technique de commande d’un moteur BLDC

La commande d’un moteur brushless DC s’effectue grâce au driver le moteur L6234 précédemment présenté. Ce composant permet uniquement d’apporter la puissance nécessaire au moteur. Les trois signaux nécessaires à son fonctionnement sont générés par le microcontrôleur. Ce sont trois signaux de type PWM qui permettent de commander le moteur en position. Un trinôme de valeur permet de positionner le moteur. Il n’y a pas de point de référence : Habituellement, pour effectuer un asservissement, on place un capteur à effet hall sur l’axe du moteur. Le type de moteur utilisé permet de s’affranchir de cette contrainte matérielle.

Ces valeurs de PWM sont générées grâce à un tableur comme le montre l’illustration ci-dessous.

Cette technique de « Lookup table » permet d’éviter d’effectuer des calculs au niveau du microcontrôleur. Pour effectuer les premiers tests, nous avons dans un premier temps généré une table contenant 71 valeurs. Les moteurs utilisés possèdent 7 trinômes d’enroulements ce qui permet d’obtenir 497 pas pour 360 degrés ce qui représente une précision de 0,72 degrés. Pour augmenter la précision, il suffit de générer plus de valeurs (avec une limite de 255 valeurs : résolution des PWM configurées sur 8 bits).

Remarque : L’utilisation de signaux PWM pour la commande des ces moteurs peut provoquer des perturbations sonores en fonction de la fréquence. Pour que ces perturbations ne soient pas perceptibles par l’humain, des tests on montré qu’une fréquence de 18 KHz convient.


22

## 6.4. Modélisation des fonctions

La spécification de chaque fonction se trouve dans le cahier de spécifications.

### 6.4.1. Configuration du capteur

La configuration du capteur est une fonction essentielle au bon fonctionnement du système. En effet, la stabilisation du système se base uniquement sur les données issues du capteur. Il est donc nécessaire de le configurer correctement. Après étude de la datasheet et du référentiel des registres du capteur nous avons identifié les points suivants à configurer. Cette partie présente la marche à suivre pour l’implémentation.

Remarque : La datasheet du MPU-9250 et la référence des registres se trouvent en annexe.

6.4.1.1. Configuration accéléromètre et gyroscope : Les offsets

Les offsets permettent d’ajouter une valeur d’offset directement dans le capteur. Nous avons décidé de ne pas utiliser cette solution pour gérer ces valeurs directement au niveau du microcontrôleur.

- Offsets du gyroscope (0x13 à 0x18) : XG_OFFSET_H, XG_OFFSET_L, YG_OFFSET_H, YG_OFFSET_L, ZG_OFFSET_H, ZG_OFFSET_L
- Offsets de l’accéléromètre (0x77 à 0x7E) : XA_OFFSET_H, XA_OFFSET_L, YA_OFFSET_H, YA_OFFSET_L, ZA_OFFSET_H, ZA_OFFSET_L
6.4.1.2. Configuration accéléromètre et gyroscope : L’échelle

Les échelles pour définissent la plage d’utilisation du capteur. Les valeurs de configuration de ces échelles seront à définir lors des tests.

- Échelle du gyroscope (GYRO_CONFIG : 0x1B) : Bit 3 et 4 (GYRO_FS_SEL)
- Échelle de l’accéléromètre (ACCEL_CONFIG : 0x1C) : Bit 3 et 4 (ACCEL_FS_SEL)
6.4.1.3. Configuration de l’accès au magnétomètre

Le capteur MPU-9250 est divisé en deux
partie : Un capteur gyroscope + accéléromètre et un magnétomètre. Le
schéma ci-contre présente son architecture.

Pour accéder au magnétomètre, il existe deux solutions : La première consiste à utiliser la fonction de « Bypass » pour joindre le magnétomètre au bus i2c ce qui fait
apparaître | du | point | de | vue | du
microcontrôleur deux périphériques i2c avec deux adresses distinctes. La deuxième solution est de paramétrer le MPU-9250 pour que son magnétomètre soit accessible par des registres dédiés à des esclaves. En effet, ce capteur peut accueillir d’autres capteurs dits « esclaves » (jusqu’à 4). Avec cette solution, le microcontrôleur peut accéder à l’ensemble

23

des données du capteur avec une seule adresse i2c ce qui limite l’accès au bus. C’est cette deuxième solution qui a été choisi.

Pour effectuer la configuration du magnétomètre en tant que « esclave », il faut renseigner les registres suivants:

- I2C_SLV0_ADDR (0x25) : Adresse i2c du périphérique identifié en tant que « Esclave 0 »
- Configuration du magnétomètre : Il est nécessaire de passer par les registres de transfert de données associés à l’esclave. Les deux registres ci-dessous sont nécessaire pour effectuer la configuration de chaque registre du capteur.
- I2C_SLV0_REG (0x26) : Registre permettant de spécifier l’adresse du registre du périphérique esclave sur lequel transférer des données.
- I2C_SLV0_DO (0x63) : Valeur du registre du périphérique que l’on souhaite modifier.
- I2C_SLV0_CTRL (0x27) : Permet d’activer l’i2c et d’effectuer l’écriture.
6.4.1.4. Configuration du magnétomètre

Pour rappel, la configuration des registres du magnétomètre doit être réalisée en utilisant les registres I2C_SLV0_REG, I2C_SLV0_DO et I2C_SLV0_CTRL. En effet, le capteur n’est pas relié directement au bus i2c menant au microcontrôleur.

- Reset du capteur : AK8963_CNTL2 (0x0B) à 0x00
- Configuration : AK8963_CNTL1 (0x0A) à 0x12
- Mesures continue : Bits 0 à 3 à 0x02
- Résolution 16 bit : Bit 4 à 1

### 6.4.2. Acquisition des données

La fonction d’acquisition des données doit permettre de récupérer les données brutes issues du capteur. Elle doit donc renvoyer trois trinômes de valeur correspondants aux données du gyroscope, de l’accéléromètre et du magnétomètre.

Figure 29 : Fonction "Acquisition des données" La fonction d’acquisition des données est divisée en trois sous fonction pour dissocier chaque type de capteur.

6.4.2.1. Acquisition des données du gyroscope

L’acquisition des données du gyroscope s’effectuant en lisant 6 octets à partir de l’adresse GYRO_XOUT_H (0x43). Les données du gyroscope sont codées sur 16 bit, il est donc nécessaire d’assembler les données une fois celles-ci lues. En effet, la donnée est divisée en deux partis : GYRO_...OUT_H (pour les bits de poids fort) et GYRO_...OUT_L (pour les bits de poids faible).

Acquisition des données

/

/

/

i2c

accel [3]

gyro [3]

mag [3]

3

3

3

24

6.4.2.2. Acquisition des données de l’accéléromètre

L’acquisition des données de l’accéléromètre est similaire à celle des données du gyroscope. Il s’agit de lire 6 octets à partir de l’adresse ACCEL_XOUT_H (0x3B). Tout comme pour le gyroscope, les données sont codées sur 2 x 8 bits, il est donc nécessaire d’assembler les deux parties après lecture.

6.4.2.3. Acquisition des données du magnétomètre

L’acquisition des données du magnétomètre est différente. Il est nécessaire d’utiliser les registres du périphérique esclave :

- I2C_SLV0_ADDR (0x25) : On spécifie l’adresse i2c du magnétomètre tout en indiquant qu’on souhaite effectuer une lecture : 0x0C.
- I2C_SLV0_REG (0x26) : On indique l’adresse à partir de laquelle on souhaite effectuer la lecture : AK8963_XOUT_L (0x03).
- I2C_SLV0_CTRL (0x27) : On active l’i2c et demande la lecture de 6 octets : 0x87.
- On effectue une lecture de 6 octets à partir de l’adresse EXT_SENS_DATA_00 qui contiennent les données codées sur 16 bit des 3 axes du magnétomètre.

### 6.4.3. Calibration du capteur

Le capteur doit être calibré pour que les données puissent être fiables. Chaque composant du capteur nécessite une calibration particulière. C’est grâce à ces données de calibration que l’on obtient les offsets à appliquer.

6.4.3.1. Calibration du gyroscope et de l’accéléromètre

Pour la calibration du gyroscope et de l’accéléromètre, on constitue un échantillon de données que l’on va ensuite moyenner. L’acquisition de cet échantillon doit se faire lorsque le capteur est immobile.

- Pour un gyroscope, lorsqu’il est statique, celui-ci doit renvoyer 0 sur les trois axes. La moyenne de l’échantillon correspondra donc à l’offset à appliquer et ceci pour chaque axe.
- Pour un accéléromètre, lorsqu’il est statique, celui-ci doit renvoyer 0 sur X, Y et renvoyer 1 sur l’axe Z qui est l’axe perpendiculaire au sol. Ainsi, en effectuant la moyenne des échantillons sur les trois axes,

Figure 30 : Calibration du gyroscope et accéléromètre
6.4.3.2. Calibration du magnétomètre

La calibration du magnétomètre est différente. Elle nécessite d’orienter le capteur sur les 3 axes pour la constitution d’un échantillon suffisant de valeurs. Pour chaque axe, on doit enregistrer la valeur maximale et la valeur minimale renvoyée par le capteur lors des mouvements. Une fois les valeurs stables, on doit moyenne ces deux valeurs pour obtenir l’offset à appliquer :

offsetUVW = val\UV + val\]^ 2

Figure 31 : Calibration du magnétomètre

25

### 6.4.4. Traitement des données

Le traitement des données consiste à appliquer le filtre de Madgwick puis d’utiliser les formules permettant d’obtenir l’orientation du capteur sur Yaw, Pitch et Roll à partir des quaternions.

### 6.4.5. Correction de l’orientation

La correction de l’orientation permet de corriger l’orientation en fonction des mouvements volontaires de l’utilisateur. L’algorithme consiste à réduire au cours du temps la différence entre la position normale du système et la position obtenues pour le stabiliser.

### 6.4.6. Asservissement en position

L’asservissement en position utilise l’algorithme du PID comme décrit ci-dessous pour chaque axe.

Tous les x millisecondes, faire :

erreur = consigne - mesure

somme_erreurs += erreur

variation_erreur = erreur - erreur_précédente

commande = Kp * erreur + Ki * somme_erreurs + Kd * variation_erreur

erreur_précédente = erreur

Figure 32 : Algorithme PID - Asservissement

### 6.4.7. Commande de la motorisation

La commande de la motorisation s’appuie sur la « Lookup table » précédemment présentée. La commande de la motorisation consiste à se déplacer dans cette table pour faire tourner le moteur et donc changer l’orientation de la caméra.

## 6.5. Processus / fonctionnement

Le processus est découpé en deux partie. Une première phase d’initialisation permet de configurer le système et de préparer le fonctionnement normal. Ensuite, une routine de fonctionnement normale permet d’effectuer la stabilisation de la caméra et est constituée de plusieurs fonctions.

Remarque : Pour permettre d’effectuer l’étalonnage du capteur et le paramétrage de l’asservissement PID, le système repose sur un ensemble de paramètre. Il a été fait le choix de stocker ces paramètres en mémoire EEPROM. Cette solution à l’avantage de pouvoir modifier / mettre à jour ces valeurs pour effectuer des réglages au cours des tests. De plus, il est donc possible d’effectuer un nouvel étalonnage du capteur sans devoir modifier le code du programme.

26

### 6.5.1. Initialisation

La phase d’initialisation est une procédure qui permet d’initialiser le système. Le grafcet suivant décrit son fonctionnement. Le système utilise un grand nombre de paramètre, notamment en lien avec l’étalonnage du capteur. Ces paramètres sont chargés lors de cette phase. De plus, il est nécessaire de configurer le matériel avec notamment les interruptions (permettant de cadencer les différentes fonctions par la suite) ainsi que les entrées

/ sorties.; Vérification si calibration; effectuée; Calibration de l’accéléromètre,; gyroscope et magnétomètre 2; Chargement des; paramètres; Oui; Non; Configuration des; entrées / sorties; Configuration du capteur; interruptions; Test de communication; avec le capteur; mise en fonctionnement; Communication ok; Communication non fonctionnelle; Système paramétré; Configuration effecutée

Figure 33 : Grafcet d'initialisation

À l’issue de cette procédure d’initialisation, le système est configuré et peut entrer dans la phase de fonctionnement normale décrit ci-après.

8 | 9 | Arrêt du système Activation des moteurs et

27

### 6.5.2. Fonctionnement normal

Le fonctionnement normal du système est assuré par vecteurs d’interruptions. En effet, il a été choisi de cadencer chaque fonction en utilisant les interruptions du microcontrôleur pour s’assurer que les opérations décrites ci-dessous sont effectuées avec une fréquence constante.

Le grafcet ci-contre illustre le fonctionnement normal du système. Cette représentation correspond aux opérations à effectuer pour pouvoir effectuer la stabilisation de la caméra.

suivante :; soit 200 Hz.; Récupération des données; brutes du capteur; Application du filtre de; Madgwick; Conversion de la représentation; quaternion en Euler; Application du filtre PID; Commande de la partie; opérative

L’ensemble de ces fonctions sont cadencées de la façon

Interruption 1 : Cadencée à 200 Hz
- Récupération des données brutes du capteur
- Conversion de la représentation quaternion en Euler

Interruption 2 : Cadencée à 50 kHz
- Application du filtre PID
- Commande de la partie opérative

Interruption 3 : Cadencée à 1 kHz
- Application du filtre de Madgwick

Remarque : Le filtre de Madgwick est un algorithme itératif. Pour effectuer l’estimation de l’orientation du capteur à partir d’un échantillon de valeur, la fonction doit être appelée 5 fois. Cela signifie que la fréquence d’appel de cette fonction doit être 5 fois plus importante que celle permettant l’acquisition des données. En effectuant des tests, nous avons constaté que le microcontrôleur utilisé peut faire fonctionner ce filtre à une fréquence de 1 kHz. Nous avons donc fixé la fréquence des données à 1 KHz / 5,

Figure 34 : Grafcet de fonctionnement normal

28

## 7. Annexes

## 7.1. Liste du matériel et références

Microcontrôleur Teensy 3.1 | http://www.robotshop.com/eu/fr/platine-developpement- microcontroleur-usb-teensy-32.html
IMU 6DoF - MPU-6050 sur PCB par Drotek | http://www.drotek.com/shop/fr/home/42-mpu6050-gyro- accelerometre.html?search_query=MPU6050&results=18

IMU 9 DoF – MPU-9250 sur PCB par Drotek http://www.drotek.com/shop/fr/home/421-mpu9250-gyro-
| accelerometre- magnetometre.html?search_query=MPU9250&results=3
Moteur Brushless GBM3508-130 | http://www.drotek.com/shop/fr/home/167-moteur- brushless-nacelle-gbm3508-130.html
Breakout Board L6234 par Drotek | http://www.drotek.com/shop/fr/home/212-controleur- nacelle-brushless-l6234.html
Batterie LIPO 2200 mAh | http://www.drotek.com/shop/fr/home/313-batterie-lipo- kypom-2200mah-3s-35c.html
Driver de moteur Brushless L6234 | http://www.rs- particuliers.com/WebCatalog/Circuit_integre_pour_comman de_moteur__Driver_de_moteur_triphase__PDIP_20- 8111016.aspx

## 7.2. Références

- Comparaison de différents algorithmes IMU : http://www.olliw.eu/2013/imu-data-fusing/
- Implémentation des algorithmes de Madgwick : https://github.com/kriswiner
- Commande d’un moteur BLDC : http://www.berryjam.eu/2015/04/driving-bldc-gimbals-at-super-slow-speeds-with-arduino/

## 7.3. Ressources : Liens Git Hub

- Exemple sur 2 axes avec un filtre de Kalman :

https://github.com/bibi03331/PFE-Polytech/tree/master/Developpement/Livrables/Exemple_2_axes_kalman

- Exemple sur 2 axes avec un filtre complémentaire :

https://github.com/bibi03331/PFE-Polytech/tree/master/Developpement/Livrables/Exemple_2_axes_filtre_complementaire

- Commande d’un moteur BLDC :

https://github.com/bibi03331/PFE-Polytech/tree/master/Developpement/Livrables/Commande_moteur_brushless

29

- Commande d’un moteur BLDC comme servo en c natif :

https://github.com/bibi03331/PFE-Polytech/tree/master/Developpement/Livrables/Commande_moteur_brushless_servo_c_natif

- Exemple d’étalonnage du gyrosocope et accéléromètre :

https://github.com/bibi03331/PFE-Polytech/tree/master/Developpement/Livrables/Etalonnage_gyro_acc

- Exemple d’étalonnage du magnétomètre :

https://github.com/bibi03331/PFE-Polytech/tree/master/Developpement/Livrables/Etalonnage_mag

- Exemple d’étalonnage du capteur complet :

https://github.com/bibi03331/PFE-Polytech/tree/master/Developpement/Livrables/Etalonnage_gyro_acc_mag

- Asservissement en positition (PID) :

https://github.com/bibi03331/PFE-Polytech/tree/master/Developpement/Livrables/Asservissement_en_position

- Exemple d’acquisition des données brutes du capteur :

https://github.com/bibi03331/PFE-Polytech/tree/master/Developpement/Livrables/Acquisition_donnees_brutes

## 7.4. Conception mécanique : Mises en plan 9 12

FINITION:; ECHELLE:1:1; FEUILLE 1 SUR 1

SAUF INDICATION CONTRAIRE:
LES COTES SONT EN MILLIMETRES
ETAT DE SURFACE:
TOLERANCES:
LINEAIRES:
ANGULAIRES:

NE PAS CHANGER L'ECHELLE CASSER LES
REVISION ANGLES VIFS

NOM | SIGNATURE | DATE | | | | TITRE:

AUTEUR
VERIF.
APPR.
FAB.
QUAL. | | | | MATERIAU: | Bielle pitch MASSE: No. DE PLAN | A4

ECHELLE:1:2; FEUILLE 1 SUR 1; NE PAS CHANGER L'ECHELLE; REVISION; CASSER LES; FINITION:; ANGLES VIFS

SAUF INDICATION CONTRAIRE:
LES COTES SONT EN MILLIMETRES
ETAT DE SURFACE:
TOLERANCES:
LINEAIRES:
ANGULAIRES:

NOM | SIGNATURE | DATE | | | | TITRE:

AUTEUR
VERIF.
APPR.
FAB.
QUAL. | | | | MATERIAU: | Bielle roll MASSE: No. DE PLAN | A4

ECHELLE:1:1; FEUILLE 1 SUR 1; NE PAS CHANGER L'ECHELLE; REVISION; ANGLES VIFS; FINITION:; CASSER LES

SAUF INDICATION CONTRAIRE:
LES COTES SONT EN MILLIMETRES
ETAT DE SURFACE:
TOLERANCES:
LINEAIRES:
ANGULAIRES:

NOM | SIGNATURE | DATE | | | | TITRE:

AUTEUR
VERIF.
APPR.
FAB.
QUAL. | | | | MATERIAU: | Bielle yaw MASSE: No. DE PLAN | A4

ECHELLE:1:2; FEUILLE 1 SUR 1; NE PAS CHANGER L'ECHELLE; REVISION; CASSER LES ANGLES VIFS; SAUF INDICATION CONTRAIRE:; FINITION:

LES COTES SONT EN MILLIMETRES
ETAT DE SURFACE:
TOLERANCES:
LINEAIRES:
ANGULAIRES:

NOM | SIGNATURE | DATE | | | | TITRE:

AUTEUR
VERIF.
APPR.
FAB.
QUAL. | | | | MATERIAU: | Interface support MASSE: No. DE PLAN | A4

ECHELLE:1:1; FEUILLE 1 SUR 1; NE PAS CHANGER L'ECHELLE; REVISION; CASSER LES ANGLES VIFS; SAUF INDICATION CONTRAIRE:; FINITION:

LES COTES SONT EN MILLIMETRES
ETAT DE SURFACE:
TOLERANCES:
LINEAIRES:
ANGULAIRES:

NOM | SIGNATURE | DATE | | | | TITRE:

AUTEUR
VERIF.
APPR.
FAB.
QUAL. | | | | MATERIAU: | Renfort interface MASSE: No. DE PLAN | A4

35

## 8. Table des figures

36

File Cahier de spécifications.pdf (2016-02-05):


## École Polytechnique de l’Université de Tours

64, Avenue Jean Portalis
37200 TOURS, France
Tél. +33 (0)2 47 36 14 14

## www.polytech.univ-tours.fr

# Département Informatique industrielle

# Cahier de spécifications

Projet : | Système de stabilisation motorisé pour caméra
Réalisé par : | Sébastien LAPORTE | Encadré par : | Ameur SOUKHAL
Début du projet : | 22/09/2015 | Fin du projet : | 10/02/2015

Historique des modifications

Version | Date | Note de version
1.0 | 14/11/2015 | Version de dépôt initial

Cahier de spécifications | Système de stabilisation motorisé pour caméra

## TABLE DES MATIERES

Cahier de spécifications | Système de stabilisation motorisé pour caméra

Cahier de spécifications | Système de stabilisation motorisé pour caméra

Cahier de spécifications | Système de stabilisation motorisé pour caméra

### 1. INTRODUCTION

Ce document a pour objectif de définir les besoins, l’environnement et les objectifs pour la réalisation du projet de fin d’étude à Polytech Tours. Ce document décrit également le découpage des tâches effectué avec un planning prévisionnel et identifie les différents livrables permettant de valider les étapes au cours du projet. Le porteur du projet qui agit également en tant que MOE est Sébastien Laporte, étudiant en cinquième année de cycle d’ingénieur en informatique industrielle. L’encadrant du projet représentant la MOA est Monsieur Ameur Soukhal, enseignant chercheur au CNRS.

### 2. CONTEXTE DE LA REALISATION

### 2.1. CONTEXTE

Depuis quelques années, le marché des caméras d’action est en constante évolution. C’est la marque GoPro qui a démocratisé ce type de matériel et qui s’est imposée comme leader dans le domaine. Grâce à cette gamme de caméra, il est possible de filmer ses activités sportives, sur tous les terrains avec un minimum d’encombrement. Cependant, malgré la miniaturisation et la qualité du capteur, il est souvent difficile de filmer de manière stable lorsqu’on conduit une moto ou que l’on descend une piste de ski. C’est donc dans ce contexte que la MOA propose ce projet afin de trouver une solution à ce besoin.

### 2.2. OBJECTIFS

L’objectif de ce projet est de concevoir et réaliser un système de stabilisation pour caméra d’action. Fixée sur le système, la caméra sera stabilisée de façon mécanique pour permettre à l’utilisateur de filmer tout en conservant une image stable. Cette stabilisation sera assurée par des effecteurs électriques. Sont utilisation doit être simple et intuitive.

### 2.3. EXISTANT

Certains projets ont vu le jour avec la prolifération des drones pourvus de caméras sur nacelles stabilisées. Le choix qui a été pris dans le cadre de ce projet est de considérer que le projet n’a pas d’existant ni matériel, ni logiciel.

### 2.4. BASES METHODOLOGIQUES

Souhaitant proposer une première version du système le plus tôt possible, nous avons choisi d’utiliser la méthode SCRUM, qui fait parti des méthodes agiles. Le découpage des tâches est détaillé dans la partie 8 de ce document.

### 3. DESCRIPTION GENERALE

### 3.1. ENVIRONNEMENT DU PROJET

Ce PFE s’inscrit dans un travail de recherche et développement effectué au sein de Polytech Tours afin de trouver des solutions au problème étudié. Le système à développer est totalement indépendant de tout autre projet. Il contiendra donc l’ensemble des fonctions matérielles et logicielles.


Cahier de spécifications | Système de stabilisation motorisé pour caméra

### 3.2. CARACTERISTIQUES DES UTILISATEURS

L’utilisateur doit pouvoir utiliser le produit sans aucune connaissance sur le plan informatique ou technique. Son utilisation doit être intuitive pour pouvoir être utilisée par des étudiant en école de cinéma ou des professionnels.

### 3.3. FONCTIONNALITES ET STRUCTURE GENERALE DU SYSTEME

CAS D’UTILISATION

Du point de vue de l’utilisateur, le système a pour unique fonctionnalité la stabilisation d’une caméra. Pour assurer cette fonction de stabilisation, les fonctions internes au système sont détaillées dans la partie « Description des fonctionnalités ».

Figure 1 : Cas d'utilisation

SCHEMA DU SYSTEME

Le système est composé d’une structure mécanique motorisée sur trois axes, de capteurs d’orientation et d’un système embarqué, le tout fonctionnant sur batterie. Le schéma ci-après présente la structure générale et définit le repère 3D.

Le système comporte deux capteurs : Le capteur principal est fixé sur la caméra, il
permet | d’effectuer | la
stabilisation.

Le second capteur permet d’obtenir l’orientation du bâti,
et | par | conséquent,
l’orientation souhaitée par l’utilisateur.

Figure 2 : Schéma du système

Utilisateur

Système de stabilisation

Stabiliser la
caméra

Cahier de spécifications | Système de stabilisation motorisé pour caméra

### 3.4. CONTRAINTES DE DEVELOPPEMENT

- Langage de programmation : Langage C
- Traitement des données : Une étude préliminaire a permis d’identifier le type de capteur à utiliser pour acquérir l’orientation dans l’espace : Un capteur IMU 9DOF. Les données issues d’un tel capteur devront être filtrées et traitées afin d’obtenir l’orientation de la caméra sur les 3 axes : X, Y et Z. Il sera donc nécessaire de choisir et d’implémenter un algorithme pour obtenir les informations d’orientation qui sont un prérequis à la stabilisation du système. Ce travail de recherche sera effectué avec la tâche « Étude bibliographique ».
- Besoin important en ressources de calcul : Les algorithmes de traitement des données issues d’un capteur 9 axes (gyroscope, accéléromètre, magnétomètre) impliquent une forte demande en calculs. Le microcontrôleur devra être choisi en fonction de cette contrainte.
- Faible poids et encombrement : Le système doit être utilisable par un utilisateur en le portant à une seule main. Son poids devra donc être contenu pour qu’il puisse être utilisé sans fatiguer son porteur. De plus, l’encombrement du système doit être réduit pour qu’il puisse être fixé sur une moto ou autre engin motorisé. Ces deux contraintes seront à prendre en compte lors de la conception mécanique.
- Alimentation autonome : L’autonomie est un point important de ce système qui doit être utilisable pendant plus d’une heure sans changer de batterie. Cette contrainte devra être prise en compte lors du dimensionnement de la partie alimentation.
- Prix : Le coût de l’ensemble des composants doit être limité pour que le projet soit viable. On trouve aujourd’hui des systèmes de stabilisation pour ce type de caméra aux alentours des 300€. Le coût de l’ensemble du système devra s’approcher au mieux de cette somme.

Cahier de spécifications | Système de stabilisation motorisé pour caméra

### 4. DESCRIPTION DES INTERFACES EXTERNES

### 4.1. INTERFACES MATERIEL / LOGICIEL

- Bus I2C : Le capteur IMU utilise une liaison I2C pour communiquer avec le microcontrôleur. Sur cette liaison transitent les données de l’accéléromètre, du gyroscope et du magnétomètre.
- Moteurs brushless : La commande de ce type de moteur se fait par 3 signaux PWM.

### 4.2. INTERFACES HOMME / MACHINE

Le fonctionnement du système ne requiert pas d’interface homme / machine. Seul un interrupteur de mise sous tension permet la mise en route du système. Cependant, l’orientation de la caméra se fait en fonction du comportement de l’utilisateur.

Le système étant stabilisé, celui-ci tend à compenser l’orientation de la caméra pour la conserver dans une certaine position définie. Cependant, l’utilisateur a la possibilité de modifier l’orientation de la caméra en agissant sur l’orientation du système. En effet, par nature, la stabilisation compense les mouvements intempestifs de la caméra. Si l’utilisateur adopte un mouvement qui tend à changer l’orientation de la caméra, le système va alors s’adapter et corriger sa position de stabilisation.

L’utilisateur a la possibilité de modifier l’orientation de la caméra sur les axes Pitch et Yaw. On ne souhaite pas modifier l’axe Roll car celui-ci est perpendiculaire au sol, ce qui produirait un angle de vidéo indésirable. Le schéma ci-après présente l’interaction de l’utilisateur avec le système.


Cahier de spécifications | Système de stabilisation motorisé pour caméra
Correction sur X : Pitch | Correction sur Z : Yaw

Figure 3 : Correction sur l'axe X par l'utilisateur

Figure 4 : Correction sur l'axe Z par l'utilisateur

Cette correction permet à l’utilisateur d’incliner la caméra de bas en haut et de haut en bas. L’utilisateur est limité à plus ou moins 35 degres pour continuer à assurer une stabilisation (qui nécessite une amplitude de mouvement).

Cette correction permet à l’utilisateur de faire pivoter la caméra de gauche à droite et de droite à gauche. Il n’y a aucune limite de mouvement sur cet axe.

### 4.3. INTERFACES LOGICIEL / LOGICIEL

Le système a pour vocation d’être entièrement autonome. Celui-ci ne s’interface donc avec aucun logiciel. En effet, l’ensemble des réglages sont effectués dès la conception du système. Celui-ci étant conçu pour une seule caméra, il n’est pas nécessaire de corriger des paramètres au cours la vie du système.

Captage; Traitement; Acquisition / traitement des données; Asservissement de la position; Commande des moteurs; Partie opérative; Grandeurs physiques; Bus i2c; Données brutes de l’accéléromètre, gyroscope et magnétomètre; Consigne de correction pour chaque axe; Données brutes; Commande; Commande des 3 moteurs : 3 signaux PWM et 1 signal TOR par moteur; Orientation; Calcul de la correction de l’utilisateur

Cahier de spécifications | Système de stabilisation motorisé pour caméra

### 5. ARCHITECTURE GENERALE DU SYSTEME

Le système est composé des 3 sous-ensembles suivants : Captage, Traitement et partie opérative.

Figure 5 : Architecture du système

Ø Captage : Sous-ensemble permettant de fournir au système les données brutes nécessaires à la modélisation de l’orientation de la caméra et du système dans un espace 3D.
Ø Traitement : Sous-ensemble permettant de réaliser plusieurs fonctions : Traitement des données, calcul de la correction de l’utilisateur, asservissement en position et commande des moteurs.
- Fonction « Acquisition / traitement des données » : Permet d’obtenir l’orientation exacte de la caméra et du bâti à partir des données brutes envoyées par le sous-ensemble « Captage ».
- Fonction « Calcul de la correction de l’utilisateur » : Cette fonction permet de calculer la correction à apporter pour modifier l’orientation de la caméra en fonction de celle du bâti. C’est grâce à cette fonction que l’utilisateur a la possibilité d’agir sur l’angle Yaw et Pitch de la caméra (Présenté dans la partie 4.2).
- Fonction « Asservissement de la position » : Permet de calculer la correction à appliquer sur le sous-ensemble « Partie opérative » pour corriger l’orientation de la caméra en fonction des données produites par la fonction « Traitement des données ».
- Fonction « Commande des moteurs » : Permet d’effectuer la commande des moteurs en fonction de la consigne calculée par la fonction « Asservissement de la position ».
Ø Partie opérative : Sous-ensemble constitué d’une structure mécanique et de moteurs permettant d’orienter la caméra dans un espace 3D.

Données capteur caméra traitées : Yaw, Pitch et Roll

Données capteur bâti traitées : Yaw, Pitch et Roll

Correction à apporter sur Yaw, Pitch et Roll

Cahier de spécifications | Système de stabilisation motorisé pour caméra

### 6. DESCRIPTION DES FONCTIONNALITES

### 6.1. FONCTION D’ACQUISITION DES DONNEES

IDENTIFICATION DE LA FONCTION

- Présentation : Cette fonction permet la récupération des informations issues du capteur MPU-9250. Ce capteur intègre un accéléromètre, un gyroscope ainsi qu’un magnétomètre qui ont leurs données accessibles depuis un bus i2c. L’acquisition des données consiste à dialoguer avec le capteur en i2c pour obtenir les informations.
- Priorité : Primordiale

DESCRIPTION DE LA FONCTION

- Entrée : Cette fonction nécessite en entrée l’adresse du capteur sur le bus i2c ainsi que l’ensemble des registres nécessaires à son utilisation. L’ensemble de ces valeurs est extrait de la datasheet et disponible en annexe de ce document.
- Sortie : Cette fonction doit retourner les données de l’accéléromètre, du gyroscope et du magnétomètre sur les 3 axes : respectivement ax, ay, az, gx, gy, gz, mx, my, mz.

Figure 6 : Entrées / sorties de la fonction « Acquisition des données »

### 6.2. FONCTION DE TRAITEMENT DES DONNEES

IDENTIFICATION DE LA FONCTION

- Présentation : Les données issues du capteur sont brutes. Afin d’obtenir l’image de l’orientation du capteur, il est nécessaire d’effectuer un traitement. Cette fonction permet donc, grâce à un algorithme d’obtenir ces données.
- Priorité : Primordiale

DESCRIPTION DE LA FONCTION

- Entrée : Cette fonction prend en entrée les données brutes produites par la fonction « Acquisition des données ». Il y a donc gx, gy, gz pour les données du gyroscope, ax, ay, az pour les données de l’accéléromètre et mx, my, mz pour les données du magnétomètre.
- Sortie : Cette fonction permet d’obtenir l’orientation de la caméra au format Yaw, Pitch, Roll.

Acquisition des données

/

/

/

i2c

accel [3]

gyro [3]

mag [3]

3

3

3

Cahier de spécifications | Système de stabilisation motorisé pour caméra

Figure 7 : Entrées / sorties de la fonction « Traitement des données »

### 6.3. FONCTION DE CORRECTION DE L’ORIENTATION

IDENTIFICATION DE LA FONCTION

- Présentation : Cette fonction permet de prendre en compte les mouvements volontaires de l’utilisateur afin de modifier l’orientation de la caméra.
- Priorité : Secondaire

DESCRIPTION DE LA FONCTION

- Entrée : Cette fonction prend en entrée les données Yaw, Pitch, Roll produites par la fonction « Traitement des données » issues du capteur du bâti.
- Sortie : On obtient une correction pour les angles Yaw et Pitch.

Figure 8 : Entrées / sorties de la fonction « Correction de l'orientation »
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

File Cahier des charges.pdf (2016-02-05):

# Cahier des charges

# Projet de fin d’étude

# Steady cam

## Système de stabilisation motorisé pour caméra

Encadré par Ameur Soukhal
Proposé par Sébastien Laporte

## La demande

L’objectif du projet est de réaliser un système de stabilisation motorisé et autonome
pour caméra. Usuellement appelé | « Steady cam » | pour | « Steady camera », ce type de
matériel est utilisé notamment dans le cinéma pour réaliser des travellings fluides en absorbant les mouvements parasites. Le système doit permettre d’assurer la stabilisation de caméras d’action type GoPro.

## Contraintes du projet

- Le système doit être énergétiquement autonome
- La stabilisation doit se faire sur au moins deux axes : Roll + Pitch
- Effort de conception : Prototype avec un faible poids et encombrement
- L’utilisateur doit avoir la possibilité d’ajuster les paramètres d’amortissement
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

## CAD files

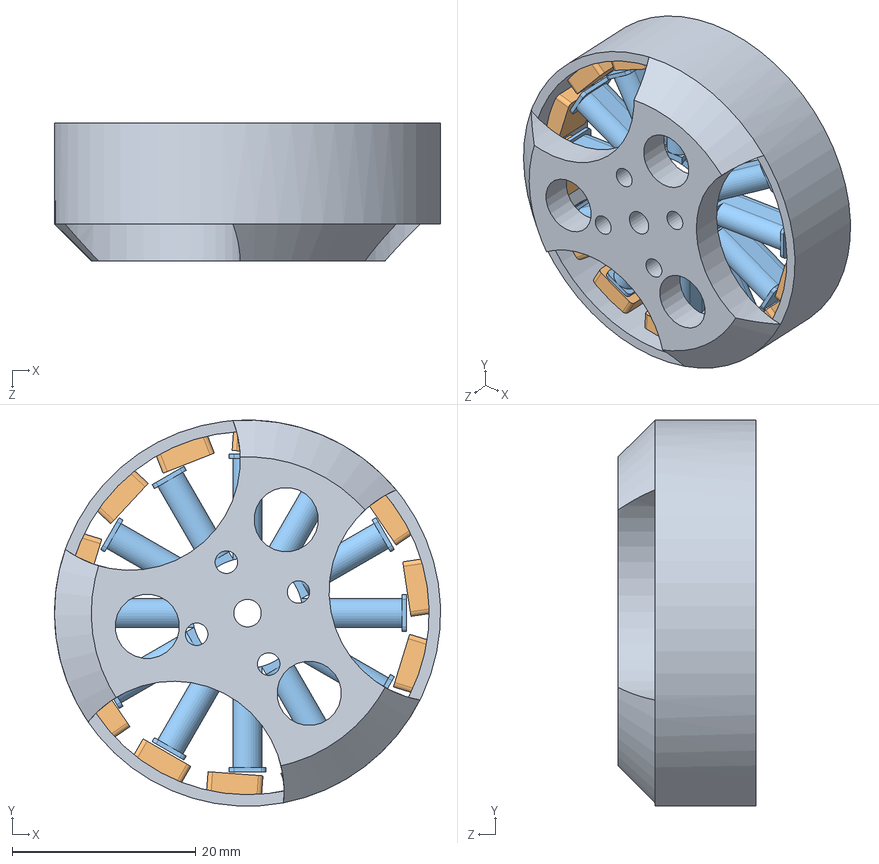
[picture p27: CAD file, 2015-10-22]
CAO_mecanique/Pièces/Moteur/Stator_GBM3508-130T.SLDASM
42.0 x 42.0 x 15.0 mm
Top
Magnet x 14
Spule x 12

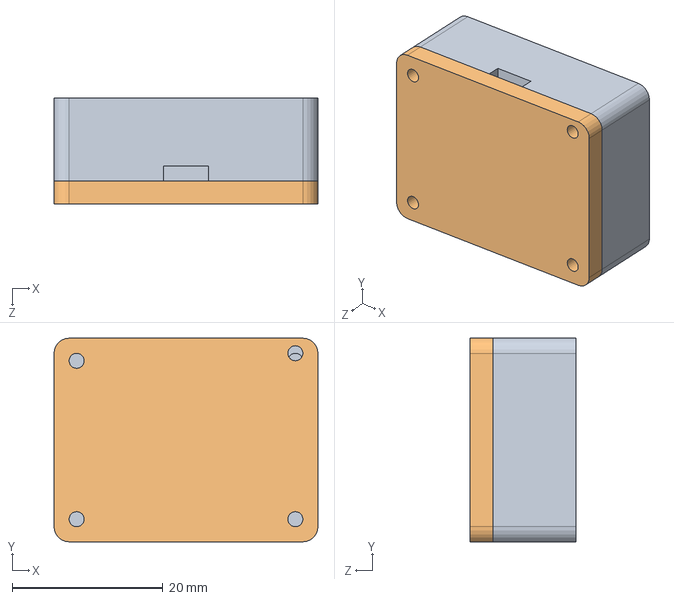
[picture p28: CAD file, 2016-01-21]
CAO_mecanique/Boitier_capteur.SLDASM
35.0 x 27.0 x 14.0 mm
Protection_capteur_fond
Protection_capteur_couvercle

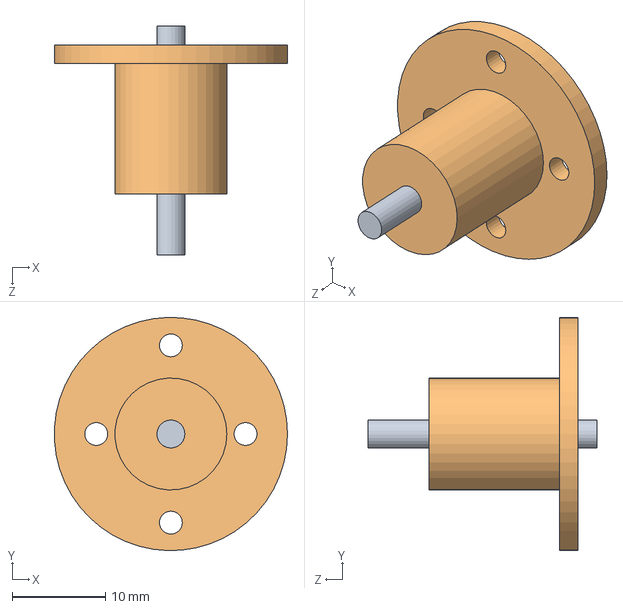
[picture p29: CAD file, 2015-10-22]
CAO_mecanique/Pièces/Moteur/Rotor_GBM3508-130T.SLDASM
25.0 x 25.0 x 24.5 mm
Wele
Bottom

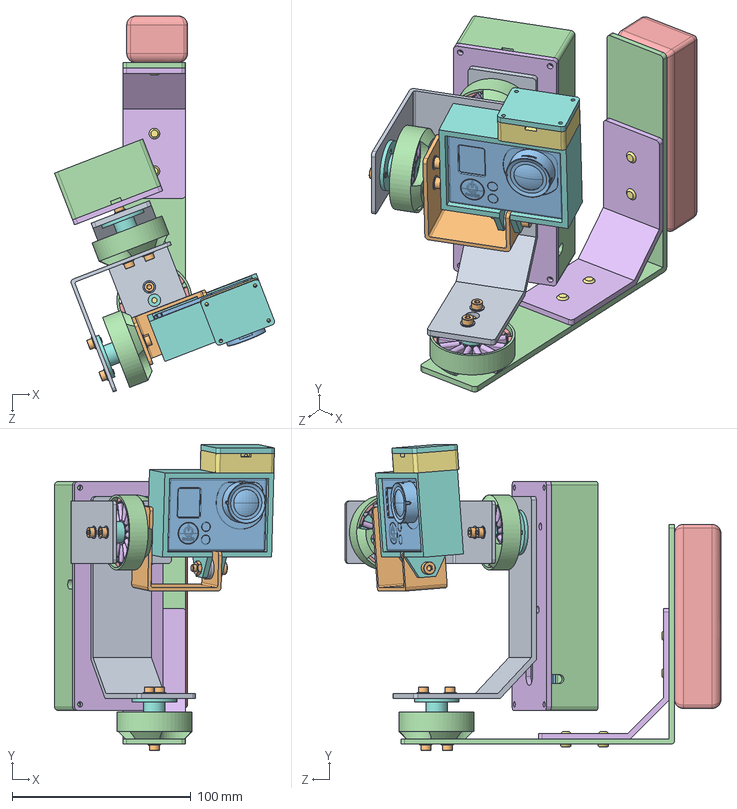
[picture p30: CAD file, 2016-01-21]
CAO_mecanique/Structure - Libre.SLDASM
123.1 x 171.2 x 210.3 mm
Bielle roll
Bielle pitch
GoPro_Hero_3
Top x 3
Magnet x 42
Spule x 36
Wele x 3
Bottom x 3
Bielle yaw
socket head cap screw_iso x 13
plain washer normal grade a_iso x 12
Interface support
Batterie
Renfort interface
Rivet x 4
Frame GoPro Hero 3
plain washer 10669 type nl_iso x 2
hex thin nut chamfered gradeab_iso
PCB
Couvercle_boitier
hex nut style 1 gradeab_iso x 4
fond_boitier
Protection_capteur_fond
Protection_capteur_couvercle

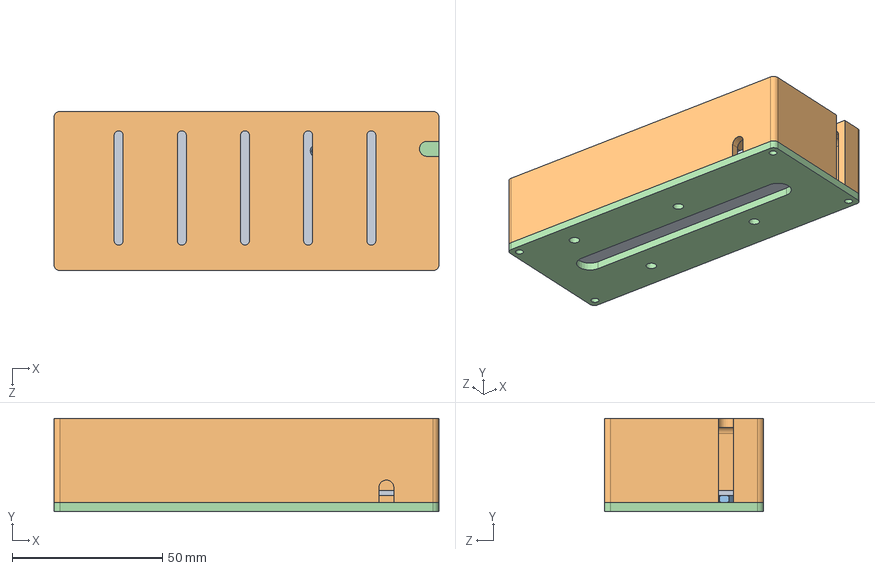
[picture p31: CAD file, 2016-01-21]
CAO_mecanique/Boitier_avec_carte.SLDASM
128.0 x 31.0 x 53.0 mm
PCB
Couvercle_boitier
hex nut style 1 gradeab_iso x 4
fond_boitier

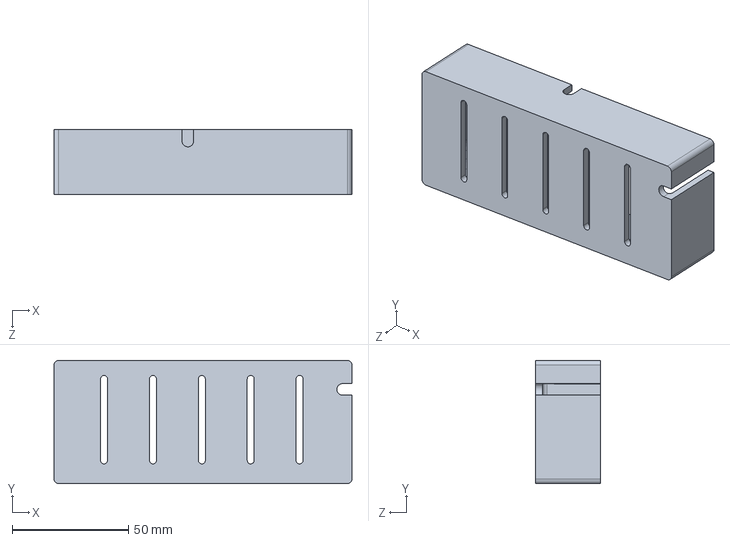
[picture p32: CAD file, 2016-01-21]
CAO_mecanique/Couvercle_boitier.SLDPRT
128.0 x 53.0 x 28.0 mm

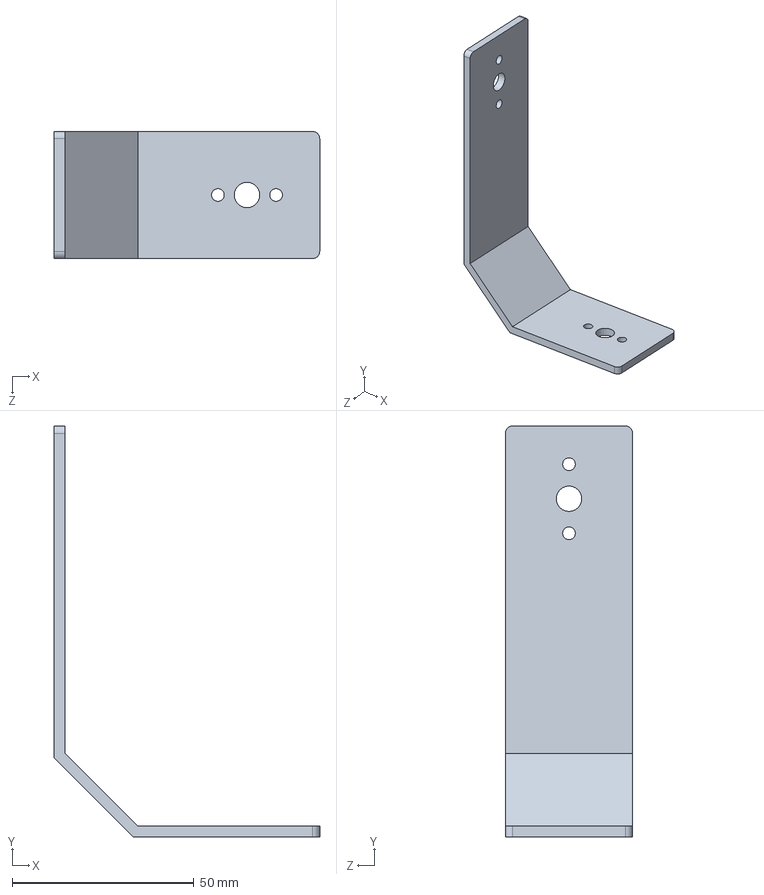
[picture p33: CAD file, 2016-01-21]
CAO_mecanique/Pièces/Bielle yaw.SLDPRT
73.0 x 113.0 x 35.0 mm

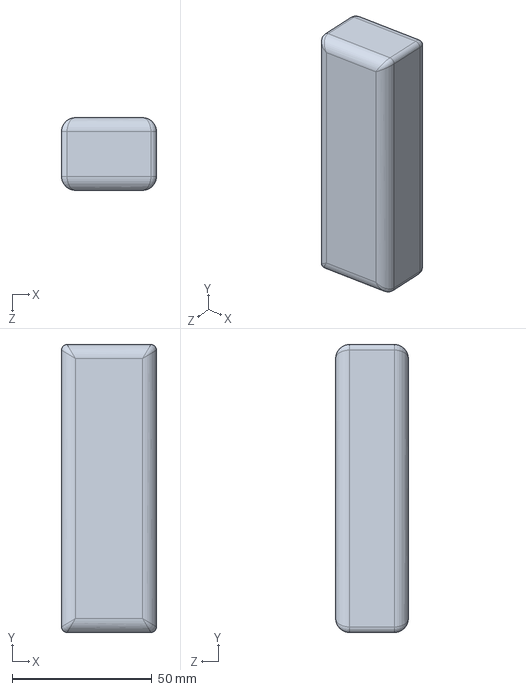
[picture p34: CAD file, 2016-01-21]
CAO_mecanique/Batterie.SLDPRT
34.0 x 103.0 x 26.0 mm

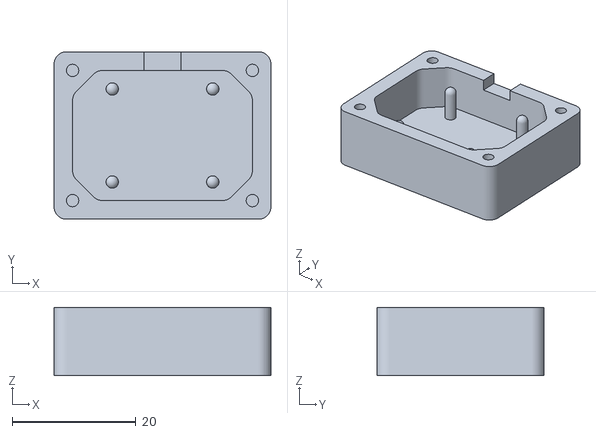
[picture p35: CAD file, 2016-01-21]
CAO_mecanique/Impression_3D/Protection_capteur_fond.STL
35.0 x 27.0 x 11.0

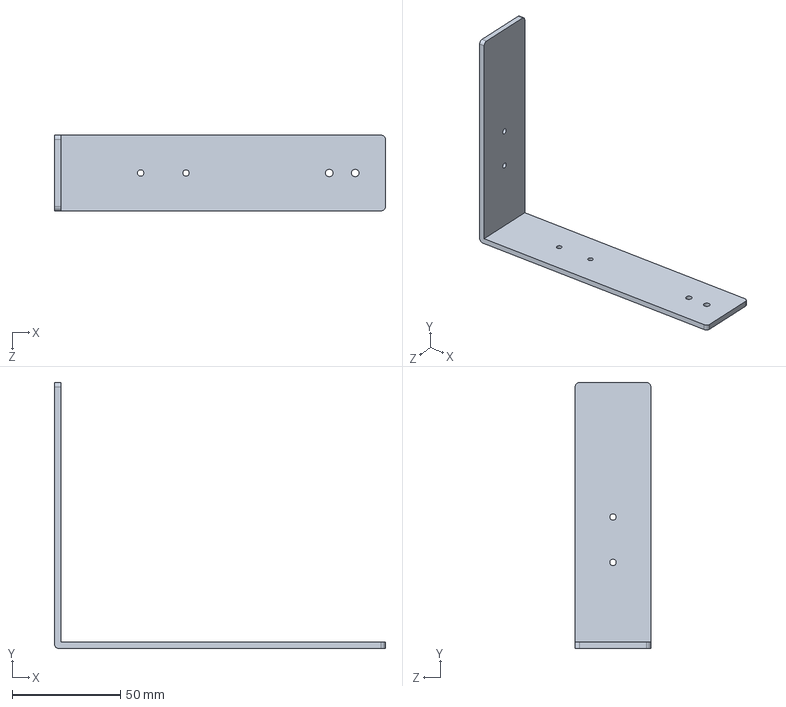
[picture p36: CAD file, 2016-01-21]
CAO_mecanique/Pièces/Interface support.SLDPRT
153.0 x 123.0 x 35.0 mm

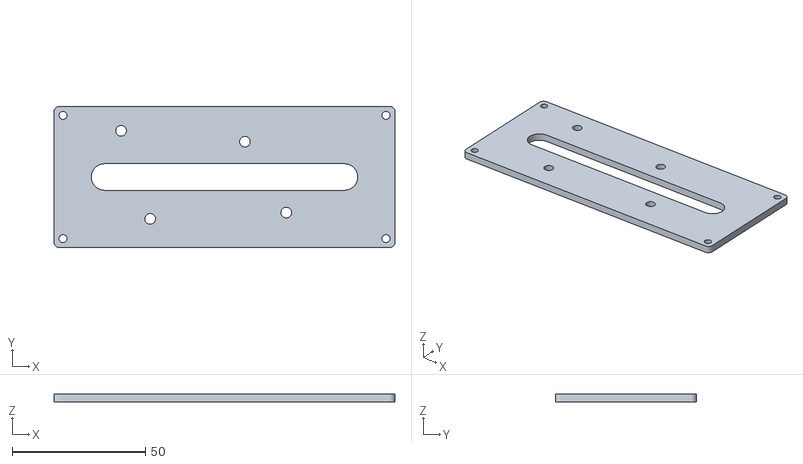
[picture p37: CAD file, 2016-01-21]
CAO_mecanique/Impression_3D/Fond_boitier.STL
128.0 x 53.0 x 3.00

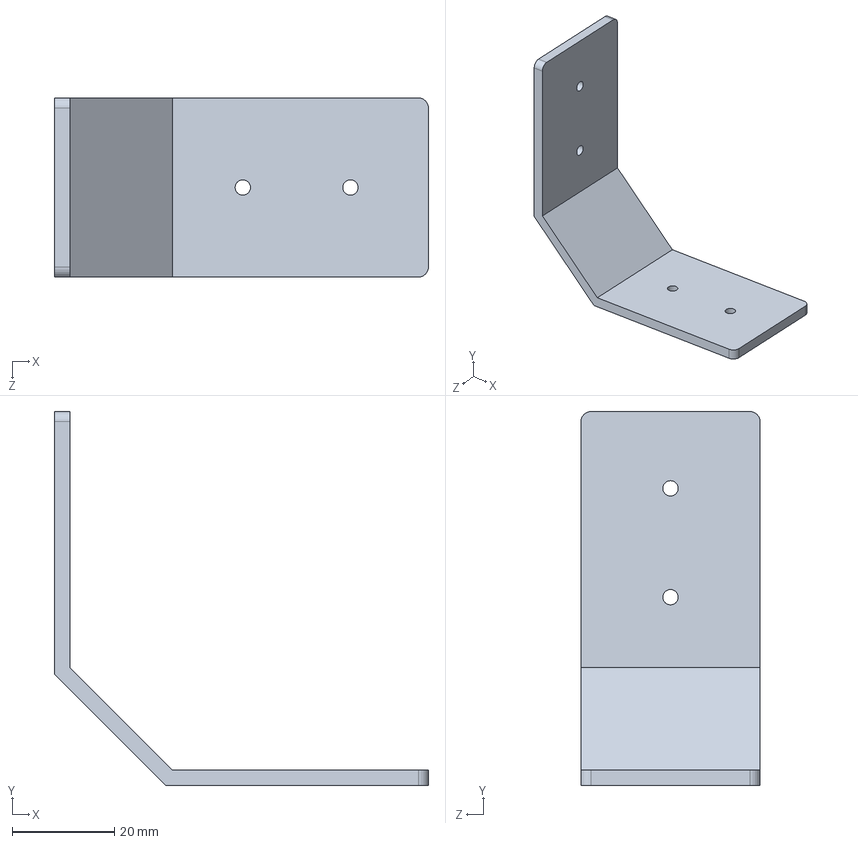
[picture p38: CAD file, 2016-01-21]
CAO_mecanique/Pièces/Renfort interface.SLDPRT
73.0 x 73.0 x 35.0 mm

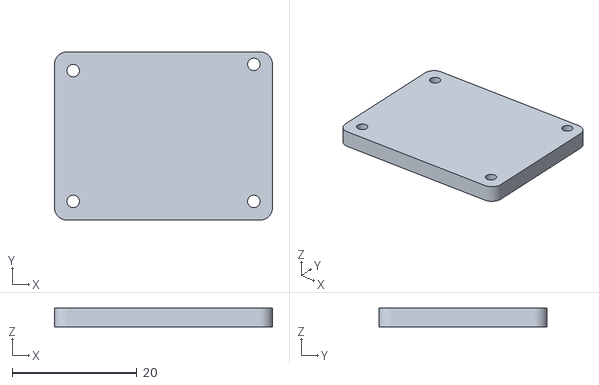
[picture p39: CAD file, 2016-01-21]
CAO_mecanique/Impression_3D/Protection_capteur_couvercle.STL
35.0 x 27.0 x 3.00

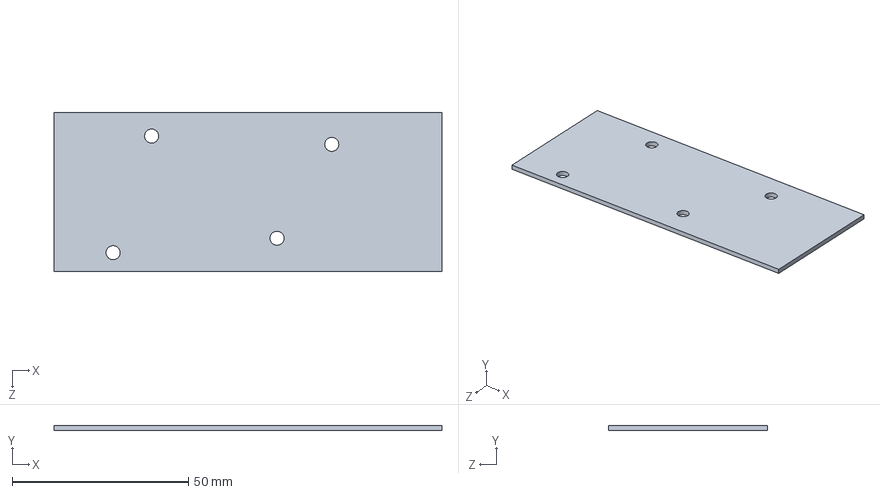
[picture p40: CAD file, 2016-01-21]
CAO_mecanique/PCB.SLDPRT
110.0 x 1.55 x 45.0 mm

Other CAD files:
CAO_mecanique/Impression_3D/Couvercle_boitier.STL
CAO_mecanique/Pièces/Moteur/Bottom.sldprt
CAO_mecanique/Pièces/Moteur/Top.sldprt
CAO_mecanique/Pièces/Protection_capteur_couvercle.SLDPRT
CAO_mecanique/GoPro_Hero_3.SLDPRT
CAO_mecanique/Pièces/Bielle pitch.SLDPRT
CAO_mecanique/Pièces/Bielle roll.SLDPRT
CAO_mecanique/Pièces/Bielle support.SLDPRT
CAO_mecanique/Pièces/Bride camera.SLDPRT
CAO_mecanique/Pièces/Equerre renfort interface.SLDPRT
CAO_mecanique/Pièces/Frame GoPro Hero 3.SLDPRT
CAO_mecanique/Pièces/Moteur/Magnet.sldprt
CAO_mecanique/Pièces/Moteur/Pièce12.SLDPRT
CAO_mecanique/Pièces/Moteur/Spule.sldprt
CAO_mecanique/Pièces/Moteur/Wele.sldprt
CAO_mecanique/Pièces/Protection_capteur_fond.SLDPRT
CAO_mecanique/Pièces/Rivet.SLDPRT
CAO_mecanique/Pièces/Support camera.SLDPRT
CAO_mecanique/Plans et photos/Bielle pitch.SLDDRW
CAO_mecanique/Plans et photos/Bielle roll.SLDDRW
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

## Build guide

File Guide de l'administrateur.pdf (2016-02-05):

1


## École Polytechnique de l’Université de Tours

64, Avenue Jean Portalis
37200 TOURS, France
Tél. +33 (0)2 47 36 14 14

## www.polytech.univ-tours.fr

# Département Informatique industrielle

# Guide de l’administrateur

Projet : | Système de stabilisation motorisé pour caméra
Réalisé par : | Sébastien LAPORTE | Encadré par : | Ameur SOUKHAL
Début du projet : | 22/09/2015 | Fin du projet : | 10/02/2015

Historique des modifications

Version | Date | Note de version
1.0 | 30/01/2016 | Version de dépôt initial

2

## Table des matières

3

## 1. Introduction

Ce document est destiné à l’administrateur du système de stabilisation motorisé pour caméra réalisé dans le cadre d’un projet de fin d’étude à Polytech Tours. Ce guide décrit les démarches à suivre pour la configuration du système.

Les configurations présentées dans ce document doivent être effectuées par l’administrateur pour préparer le système après sa fabrication. Ce paramétrage est à effectuer une seule fois dans la vie du système.

## 2. Mise en place des outils

Pour agir sur les différents paramètres du système, l’administrateur doit mettre en place l’environnement de développement constitué de l’IDE Arduino et du logiciel Teensy. Le programme développé n’utilise pas de bibliothèque externes à l’environnement Arduino.

- Page de téléchargement de l’IDE Arduino : https://www.arduino.cc/en/Main/Software
- Page de téléchargement du logiciel Teensy : https://www.pjrc.com/teensy/td_download.html

## 3. Paramètres du programme du microcontrôleur

Pour effectuer les réglages du système, l’administrateur a la possibilité d’agir sur un ensemble de paramètres. Il est possible d’afficher des valeurs dans un terminal via une liaison série, désactiver un ou plusieurs axes, agir sur les fréquences d’exécution des fonctions du système ou encore de modifier directement les valeurs liées au PID de chaque axe.

Les paramètres suivants permettent à l’administrateur d’afficher certaines informations dans un terminal série.

#define DEBUG | 0 | /* Affiche les informations d’initialisation */

#define PRINT_RAW_VALUES | 0 | /* Affiche les données brutes du capteur */

#define PRINT_YPR_VALUES | 0 | /* Affiche l’orientation de la caméra en YPR */

#define PRINT_PID_COMPUTING | 0 | /* Affiche les données de calcul du PID */

#define AXE_TO_PRINT | 0 | /* Affiche la consigne calculée d’un axe */

#define LOCK_YAW | 0 | /* Verrouillage de l’axe Yaw : Moteur immobile */

Pour effectuer ces opérations, il est nécessaire de connecter le microcontrôleur à un ordinateur et d’ouvrir le programme Arduino. L’ensemble des réglages du programme s’effectue dans le fichier nommé « parametres.h » :

## 3.1. Coefficients PID pour chaque axe (Yaw, Pitch, Roll)

Ces paramètres sont propres à la structure mécanique. Ils sont également liés aux fréquences de la boucle d’asservissement et à la fréquence de rafraichissement des données brutes du capteur. Ces coefficients peuvent être ajustés directement dans le programme ou peuvent être mis à jour depuis une application grâce au port série.

#define KP_Y 0.001 | /* kp Yaw */

#define KI_Y 0.003 | /* ki Yaw */

#define KD_Y 1.0 | /* kd Yaw */

#define KP_P 0.8 | /* kp Pitch */

#define KI_P 0.008 | /* ki Pitch */

#define KD_P 1000.0 /* kd Pitch */

#define KP_R 0.001 | /* kp Roll */

#define KI_R 0.005 | /* ki Roll */

#define KD_R 1.0 | /* kd Roll */

4

## 3.2. Activation / désactivation de chaque axe

Afin de faciliter le réglage des coefficients PID il est possible de désactiver chaque axe du système. Lorsqu’un axe est désactivé cela a pour conséquence de ne pas commander le moteur correspondant.

#define ENABLE_YAW | 1 | /* 0 : désactivation, 1 : activation */

#define ENABLE_PITCH | 1 | /* 0 : désactivation, 1 : activation */

#define ENABLE_ROLL | 1 | /* 0 : désactivation, 1 : activation */

## 3.3. Fréquence des signaux PWM pour la commande des moteurs

La modification de cette fréquence agit sur les perturbations sonores dégagées par les moteurs. En effet, si la fréquence de fonctionnement n’est pas assez importante, un sifflement se produit lors de la commande. Celleci est également en lien avec la consommation énergétique du système. Il est nécessaire de garder la fréquence le plus bas possible pour limiter la consommation. Lors de tests, nous nous sommes aperçu qu’une fréquence de 18 kHz est un bon compromis.

#define PWM_FREQUENCY | 18000 | /* Hz */

## 3.4. Fréquence de la boucle d’asservissement PID

La fréquence de cette boucle agit sur le temps de réaction du système. La modification de cette fréquence a également pour conséquence de modifier la validité des paramètres des PID.

#define PID_FREQUENCY | 50000 | /* Hz */

## 3.5. Fréquence de rafraichissement des données brutes du capteur

La fréquence de rafraichissement des données du capteur est fixée à 200 Hz par la configuration de celui-ci. L’augmentation de cette fréquence n’aura pas pour effet d’augmenter le nombre d’échantillons. En revanche, il est possible de baisser cette fréquence pour limiter le nombre d’échantillons.

#define UPDATE_CPT_FREQUENCY | 200 | /* Hz */

## 3.6. Fréquence de la boucle de l’algorithme de Madgwick

La fréquence de la boucle de l’algorithme de Madgwick est liée avec la fréquence de rafraichissement des données brutes du capteur. En effet, cet algorithme est itératif est doit avoir une fréquence 5 fois supérieur à celle du rafraichissement des données brutes du capteur pour pouvoir obtenir une estimation correcte de l’orientation.

#define MADGWICK_FREQUENCY | 1000 | /* Hz */

5

## 4. Réglage des paramètres par liaison série

Pour faciliter le réglage des coefficient PID nous avons mis en place une interface en nous appuyant sur un projet existant. Ce programme Processing permet d’agir sur les paramètres PID ainsi que d’activer ou désactiver chaque axe. Une deuxième fenêtre permet de tracer les données liées à l’asservissement.

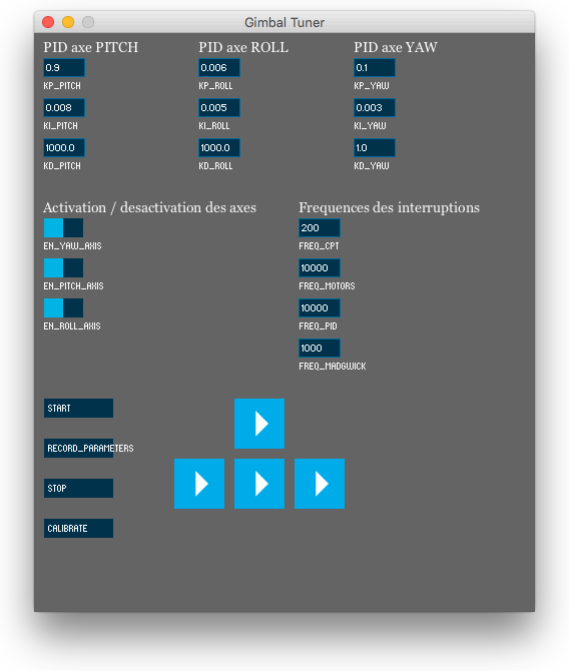
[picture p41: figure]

Figure 1 : Interface de réglage

Le programme Processing proposé peut être éventuellement remplacé par une autre solution. La mise à jour des paramètres est effectuée en transmettant l’identifiant du paramètre et sa valeur séparée par un espace tel que : « identifiant valeur ». Le tableau ci-dessous identifiant les paramètres.

Identifiant | Fonction
en_roll_axis | 0 : Désactivation de l’axe Roll | 1 : Activation de l’axe Roll
en_pitch_axis | 0 : Désactivation de l’axe Pitch | 1 : Activation de l’axe Pitch
en_yaw_axis | 0 : Désactivation de l’axe Yaw | 1 : Activation de l’axe Yaw
Kp_Roll | Paramètre KP du PID de l’axe Roll
Ki_Roll | Paramètre KI du PID de l’axe Roll

6

Kd_Roll | Paramètre KD du PID de l’axe Roll
Kp_Pitch | Paramètre KP du PID de l’axe Pitch
Ki_Pitch | Paramètre KI du PID de l’axe Pitch
Kd_Pitch | Paramètre KD du PID de l’axe Pitch
Kp_Yaw | Paramètre KP du PID de l’axe Yaw
Ki_Yaw | Paramètre KI du PID de l’axe Yaw
Kd_Yaw | Paramètre KD du PID de l’axe Yaw
freq_cpt | Fréquence de la boucle d’acquisition des données du capteur en Hz
freq_PID | Fréquence de la boucle d’asservissement en Hz
freq_madgwick | Fréquence de la boucle de l’algorithme de Madgwick en Hz

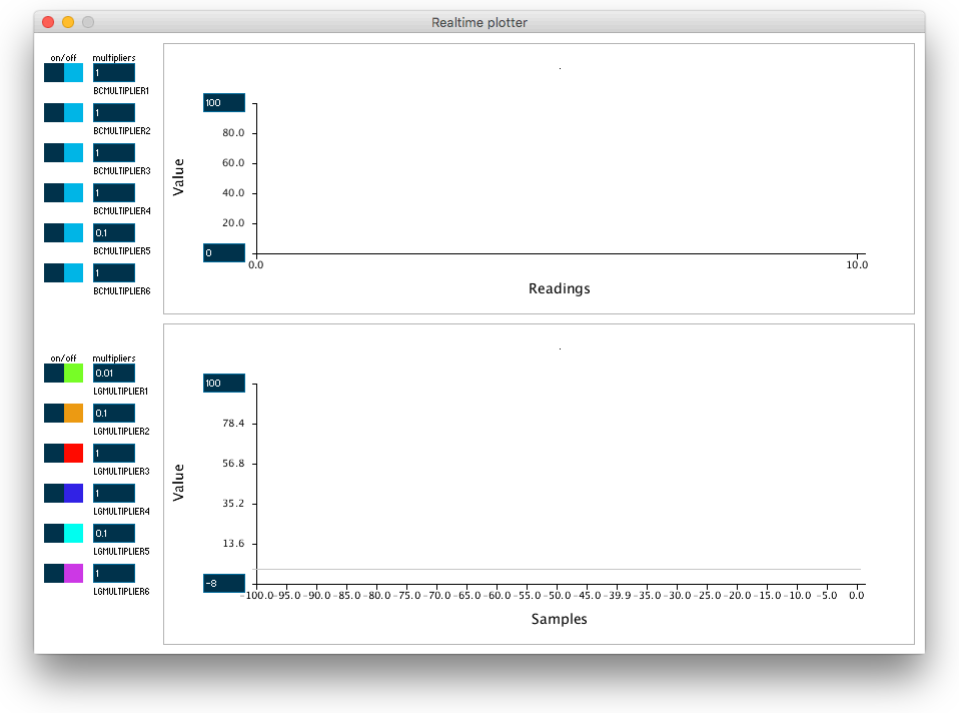
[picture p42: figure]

Figure 2 : Interface de tracée des valeurs d'asservissement L’illustration ci-dessous montre l’interface permettant d’afficher les valeurs liées à l’asservissement. Chaque axe peut donc y être représenter pour assister l’administrateur dans le réglage de l’application.

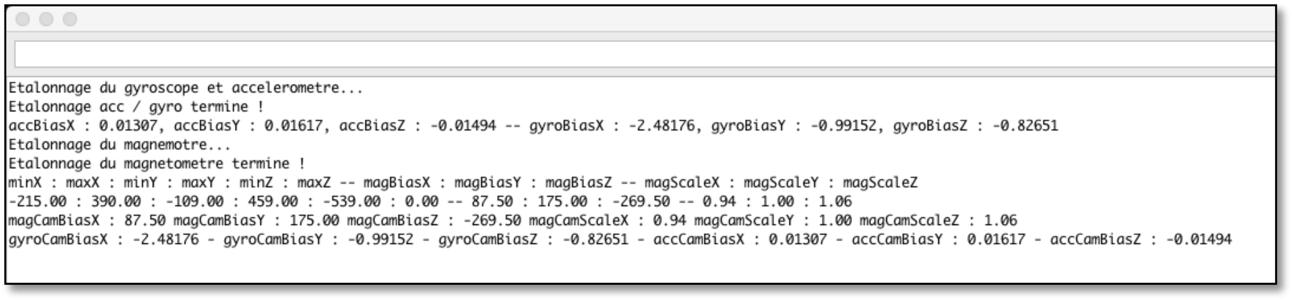
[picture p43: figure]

7

## 5. Etalonnage du capteur

Au premier démarrage du système, il est nécessaire d’effectuer la calibration du capteur MPU-9250. Une routine automatique permet d’effectuer cette calibration de façon automatique. Pour cela, il est nécessaire de connecter le microcontrôleur à un port série pour pouvoir visualiser les instructions. La vitesse de transmission est fixée à 115200 Bauds/s. La calibration s’effectue en deux phase :

- Dans un premier temps, le système va effectuer la calibration de l’accéléromètre et du gyroscope. Le système doit être stable et le capteur positionné parfaitement à l’horizontal. Une fois cette étape terminée, le système affiche les valeurs de calibration dans le terminal à titre indicatif.
- Pour terminer, le système va procéder à l’étalonnage du magnétomètre. Un message informe l’administrateur qu’il est nécessaire de réaliser des mouvements en huit avec le capteur. Pour terminer la calibration, il suffit d’immobiliser le capteur. Cette action permet de mettre fin à la procédure et d’enregistrer les valeurs de calibrations.

L’illustration ci-dessous est un exemple d’étalonnage effectué.

Figure 3 : Exemple étalonnage capteur

8

## 6. Tests

Pour vérifier la cohérence des données brutes du capteur il est possible d’afficher les valeurs dans le terminal.

- Accéléromètre : Lorsque le capteur est immobile, les valeurs doivent tendre vers 0 pour l’axe X et Y. Sur l’axe Z, la valeur doit tendre vers 1000 mG à cause de l’accélération de la pesanteur.
- Gyroscope : Lorsque le capteur est immobile, les valeurs doivent tendre vers 0 sur les trois axes.
- Magnétomètre : Les valeurs changent en fonction de la position géographique et en fonction des perturbations électromagnétiques.

9

## 7. Table des figures

## 8. Annexes

Lien Github du code source du programme : https://github.com/bibi03331/PFE-Polytech/tree/master/Developpement/Livrables/Version_finale

Lien Github du programme Processing : https://github.com/bibi03331/PFE-Polytech/tree/master/Developpement/Livrables/Console

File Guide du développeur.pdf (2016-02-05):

1


## École Polytechnique de l’Université de Tours

64, Avenue Jean Portalis
37200 TOURS, France
Tél. +33 (0)2 47 36 14 14

## www.polytech.univ-tours.fr

# Département Informatique industrielle

# Guide du développeur

Projet : | Système de stabilisation motorisé pour caméra
Réalisé par : | Sébastien LAPORTE | Encadré par : | Ameur SOUKHAL
Début du projet : | 22/09/2015 | Fin du projet : | 10/02/2015

Historique des modifications

Version | Date | Note de version
1.0 | 30/01/2016 | Version de dépôt initial

2

## Table des matières

3

## 1. Introduction

Ce document est destiné à décrire l’architecture du code du système de stabilisation motorisé pour caméra réalisé dans le cadre d’un projet de fin d’étude à Polytech Tours.

Le code source du programme est disponible en annexe par l’intermédiaire d’un lien Github.

## 2. Architecture des fichiers sources

Le programme, développé sur environnement Arduino, est découpé en six partie.

## 2.1. Programme principal

- Nom du fichier : Version_finale.ino
- Descriptif : Le fichier principal contient la boucle d’initialisation ainsi que la boucle de fonctionnement normal. Il contient également l’ensemble des fonctions nécessaires au fonctionnement du système.

Remarque : Le descriptif de chaque fonction et les paramètres associés sont décrit en commentaire dans le code.

## 2.2. Fichier de configuration

- Nom du fichier : configuration.h
- Descriptif : Contient l’ensemble des paramètres matériel du système (Adresse du capteur i2c, numéro de broche pour chaque driver de moteur, …)

## 2.3. Fichiers contenant les paramètres du système

- Nom du fichier : parameters.h
- Descriptif : Contient les paramètres logiciels du système (Coefficients PID pour chaque axe, fréquences des signaux PWM, …)

## 2.4. Le filtre de Madgwick

- Nom du fichier : quaternionFilter.ino
- Descriptif : Contient uniquement la fonction du filtre de Madgwick. La fonction prend en paramètre les données suivantes : ax, ay, az, gx, gy, gz, mx, my, mz, quaternion.
- ax, ay, az : Les données issues de l’accéléromètre pour les 3 axes (float)
- gx, gy, gz : Les données du gyroscope pour les 3 axes (float)
- mx, my, mz : Les données du magnétomètre pour les 3 axes (float)
- quaternion : Tableau contenant les 4 valeurs du quaternion (float)

## 2.5. La table des registres du capteur

- Nom du fichier : registers_map.h
- Descriptif : Contient les adresses des registres du capteur MPU-9250. Pour le détail de chaque registre, se référer à au document disponible en annexe.

4

## 2.6. Les types de données

- Nom du fichier : types.h
- Descriptif : Contient les 3 structures de données pour le fonctionnement du système. Le détail de chaque structure est décrit dans le code source.

## 3. Programmes annexes

Pour s’affranchir des librairies et de l’environnement Arduino deux programmes Arduino, également disponible en annexe permettent de mettre en œuvre la commande des moteurs et la communication i2c.

Lors des premières versions du prototype et des phases de recherche, nous avons développé différents programmes. Ils sont également en annexe de ce document.

## 3.1. Exemple de commande des moteurs brushless en c natif

- Nom du dossier : Commande_moteur_brushless_servo_c_natif
- Descriptif : Permet de configurer les sorties du microcontrôleur, d’effectuer la configuration de la fréquence des signaux PWM et de faire varier le rapport cyclique des signaux.

## 3.2. Exemple de communication i2c en c natif

- Nom du dossier : I2C_c_natif
- Descriptif : Contient l’ensemble des fonctions permettant d’effectuer la communication i2c avec le capteur MPU-9250.

## 3.3. Exemple d’acquisition des données du capteur MPU-9250

- Nom du dossier : Acquisition_donnees_brutes
- Descriptif : Programme Arduino permettant d’effectuer l’acquisition des données brutes issues du capteur MPU-9250 pour l’accéléromètre, le gyroscope et le magnétomètre.

## 3.4. Exemple de commande de moteurs brushless

- Nom du dossier : Commande_moteur_brushless
- Descriptif : Programme Arduino permettant de mettre en œuvre la commande de moteurs brushless de type BLDC.

## 3.5. Exemple d’étalonnage du capteur MPU-9250

- Nom du dossier : Etalonnage_gyro_acc_mag
- Descriptif : Routine permettant d’effectuer l’étalonnage de l’accéléromètre, du gyroscope et du magnétomètre.

## 3.6. Exemple de prototype sur 2 axes avec un filtre de Kalman

- Nom du dossier : Exemple_2_axes_kalman
- Descriptif : Programme Arduino permettant de mettre en œuvre la stabilisation d’une caméra par le biais de deux servomoteurs en utilisant un filtre de Kalman.

5

## 3.7. Exemple de prototype sur 2 axes avec un filtre complémentaire

- Nom du dossier : Exemple_2_axes_filtre_complementaire
- Descriptif : Programme Arduino permettant de mettre en œuvre la stabilisation d’une caméra par le biais de deux servomoteurs en utilisant un filtre complémentaire.

6

## 4. Annexes

Lien Github du code source du programme : https://github.com/bibi03331/PFE-Polytech/tree/master/Developpement/Livrables/Version_finale

Lien Github du programme Processing : https://github.com/bibi03331/PFE-Polytech/tree/master/Developpement/Livrables/Console

Lien Github vers l’ensemble des codes sources : https://github.com/bibi03331/PFE-Polytech/tree/master/Developpement/Livrables

Lien vers la table des registres du capteur MPU-9250 : http://43zrtwysvxb2gf29r5o0athu.wpengine.netdnacdn.com/wp-content/uploads/2015/02/MPU-9250-Register-Map.pdf

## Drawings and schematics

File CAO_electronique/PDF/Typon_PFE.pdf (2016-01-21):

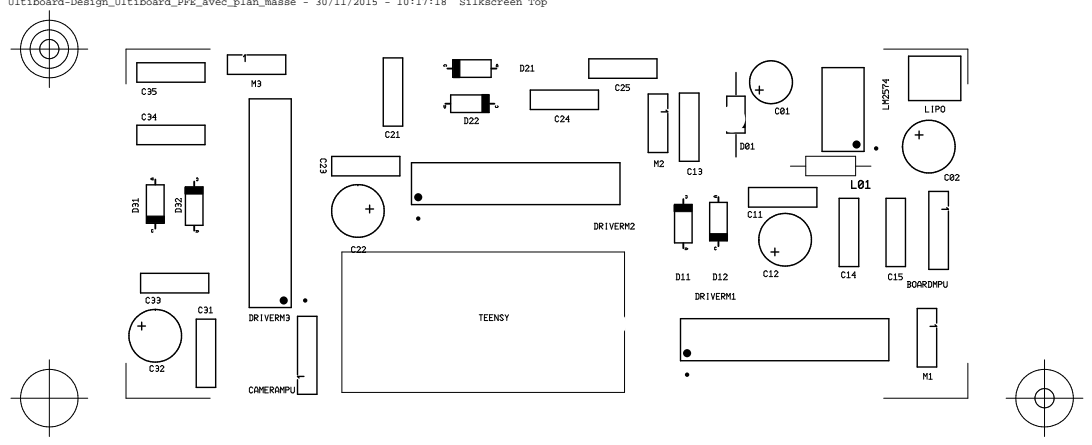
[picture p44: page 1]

Ultiboard-Design_Ultiboard_PFE_avec_plan_masse - 30/11/2015 - 10:17:18 Silkscreen Top

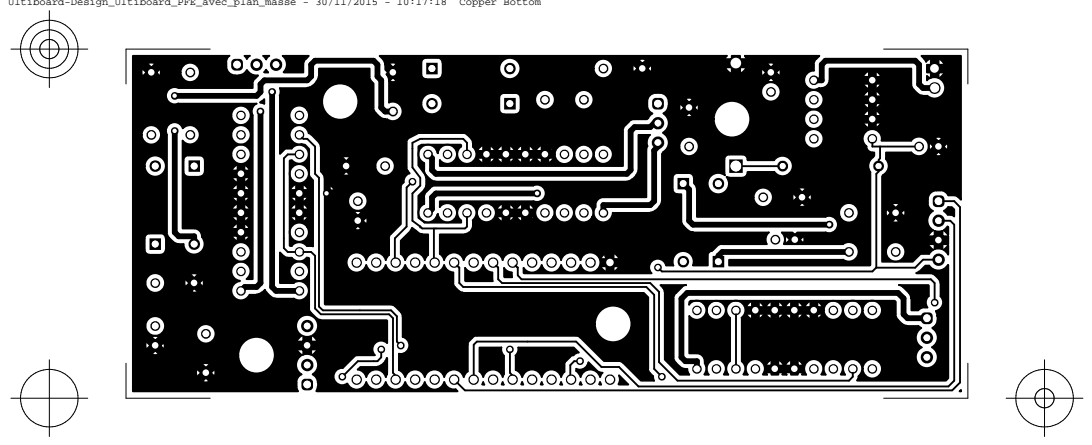
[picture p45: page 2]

Ultiboard-Design_Ultiboard_PFE_avec_plan_masse - 30/11/2015 - 10:17:18 Copper Bottom

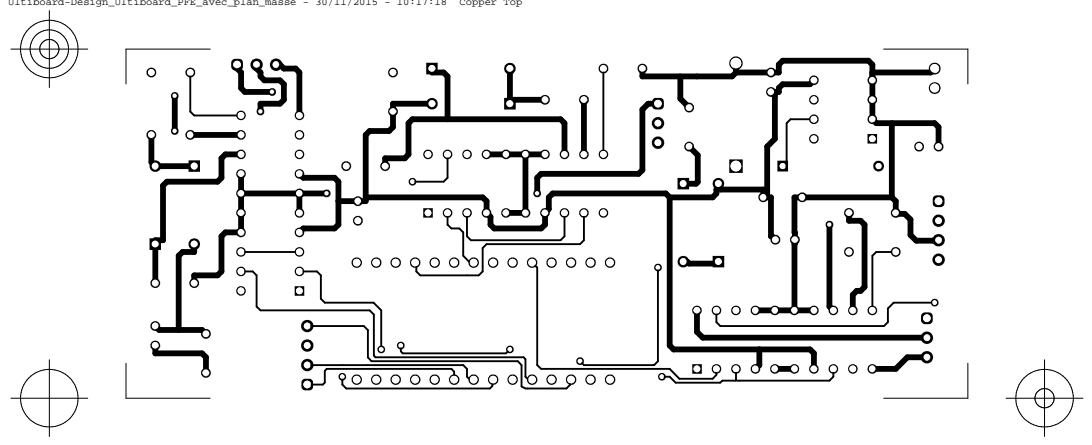
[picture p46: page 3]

Ultiboard-Design_Ultiboard_PFE_avec_plan_masse - 30/11/2015 - 10:17:18 Copper Top

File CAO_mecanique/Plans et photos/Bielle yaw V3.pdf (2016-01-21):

3,50

12

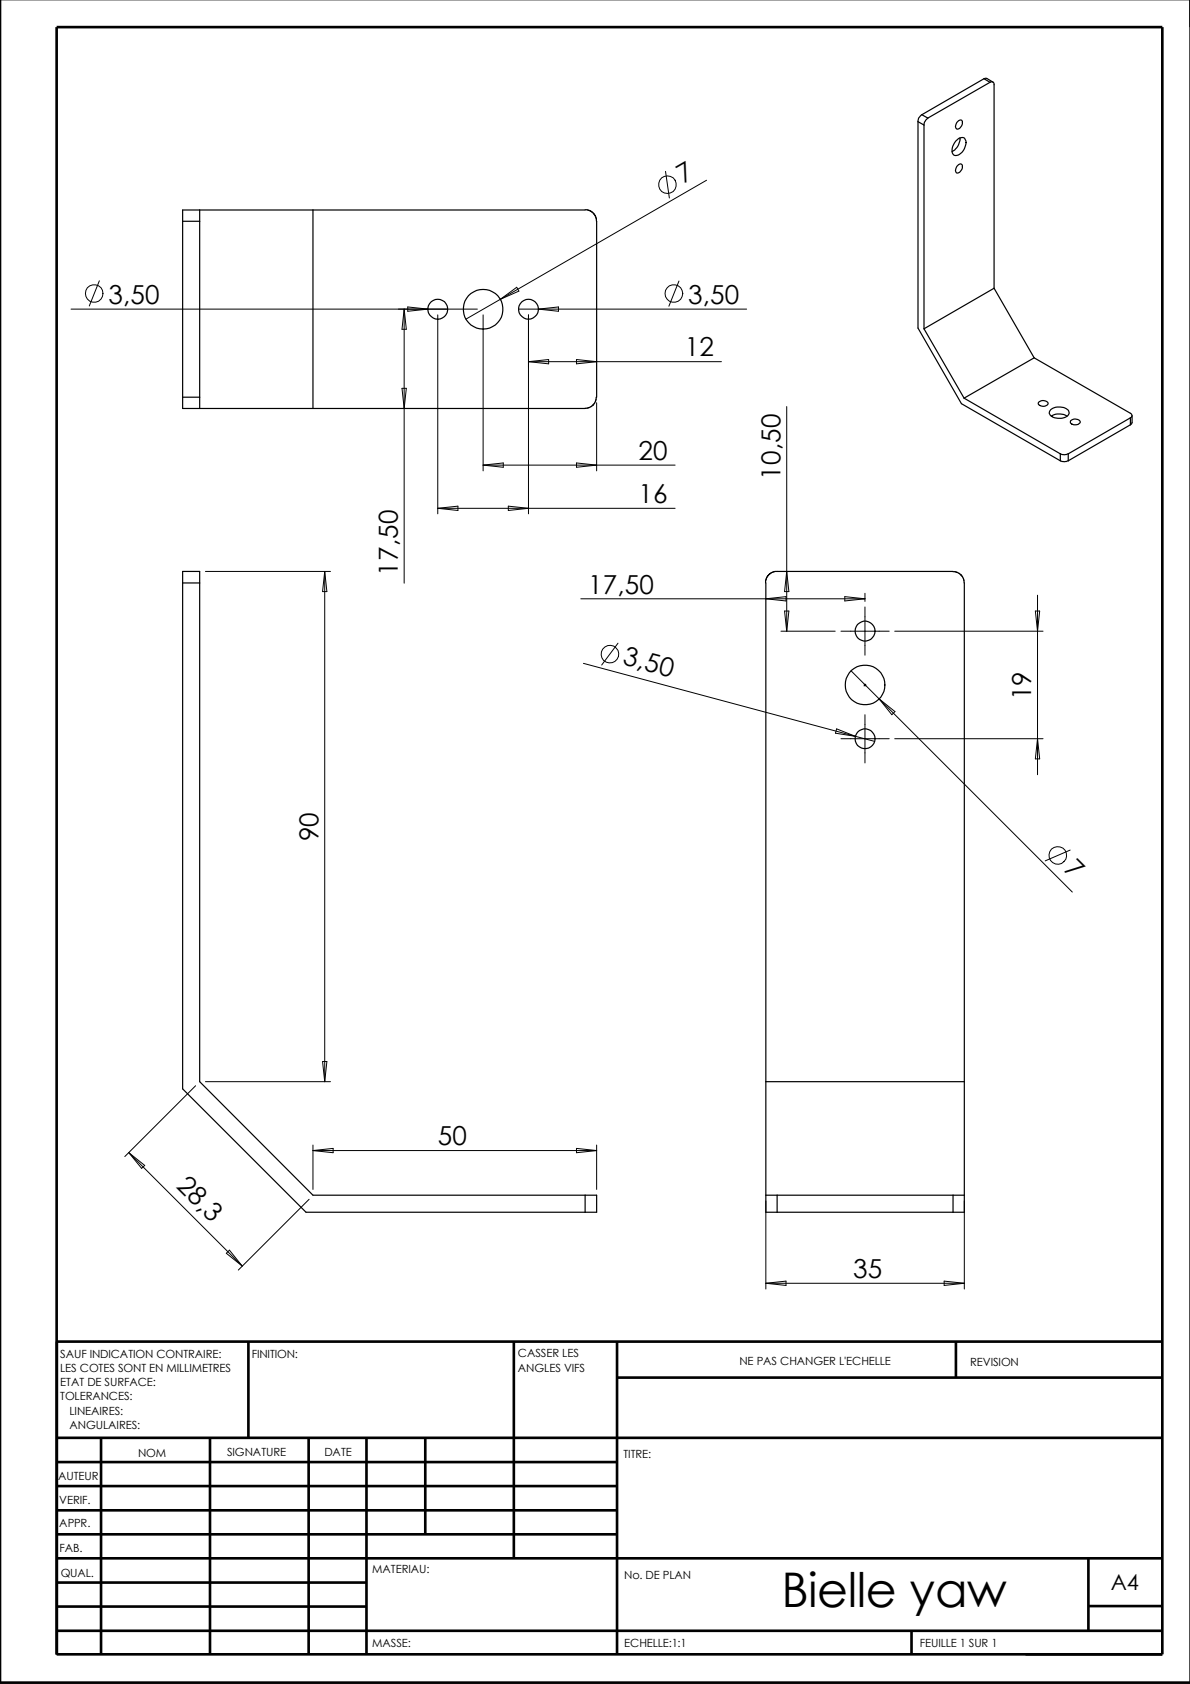
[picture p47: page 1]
MASSE:; ECHELLE:1:1; FEUILLE 1 SUR 1; NE PAS CHANGER L'ECHELLE; REVISION; ANGLES VIFS; FINITION:; CASSER LES

SAUF INDICATION CONTRAIRE:
LES COTES SONT EN MILLIMETRES
ETAT DE SURFACE:
TOLERANCES:
LINEAIRES:
ANGULAIRES:

NOM | SIGNATURE | DATE | | | | TITRE:

AUTEUR

VERIF.
QUAL. | | | | MATERIAU: | No. DE PLAN Bielle yaw | A4

APPR.

FAB.

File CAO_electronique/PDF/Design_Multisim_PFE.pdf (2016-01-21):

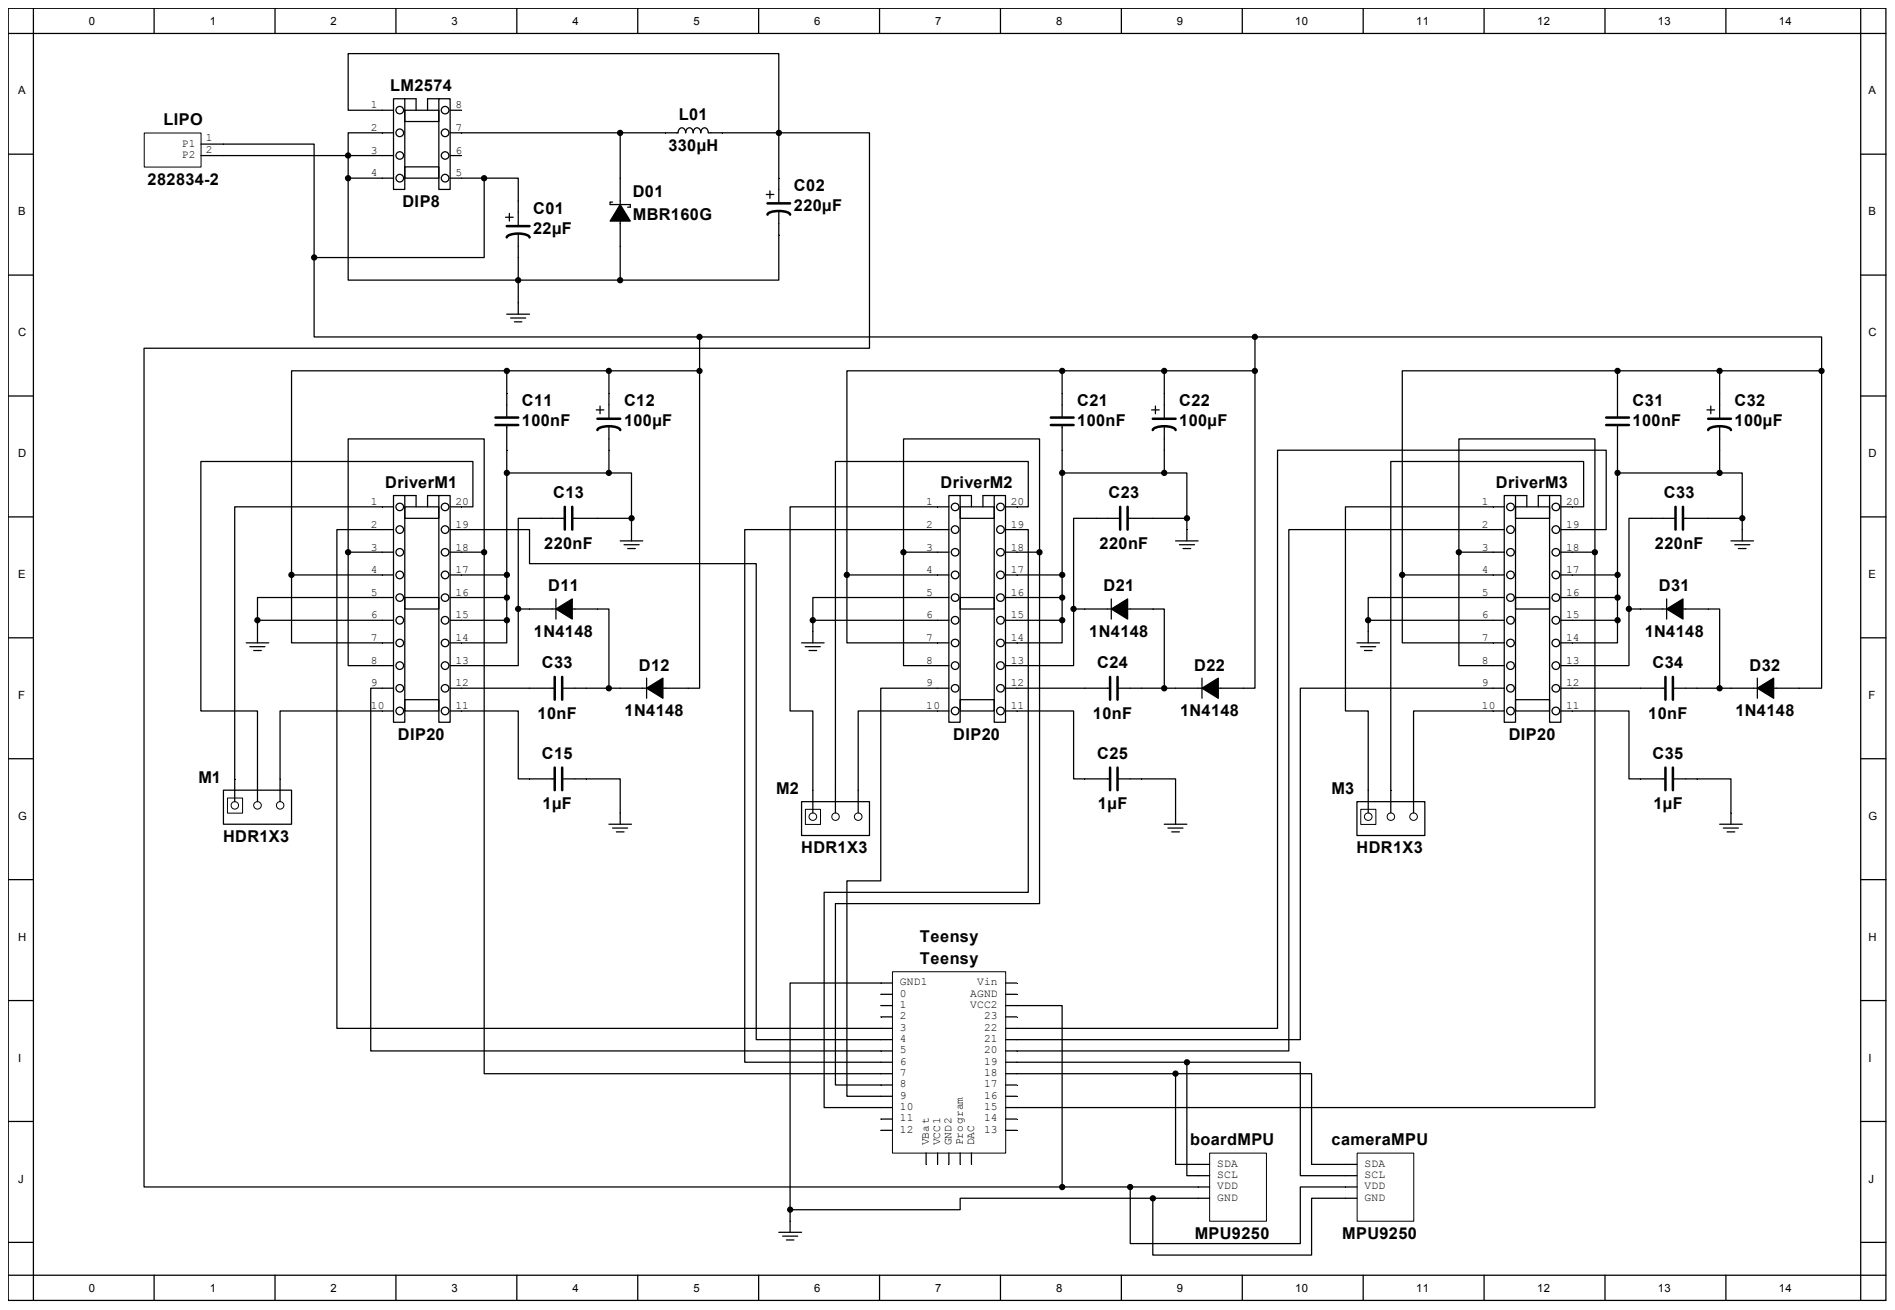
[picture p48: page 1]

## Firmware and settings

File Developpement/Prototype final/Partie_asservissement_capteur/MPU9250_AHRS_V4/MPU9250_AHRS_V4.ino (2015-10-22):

#include <Wire.h>
#include <Servo.h>

#define Kp_X 40
#define Ki_X 5
#define Kd_X 10

#define Kp_Y 40
#define Ki_Y 5
#define Kd_Y 10

#define Kp_Z 50
#define Ki_Z 10
#define Kd_Z 10

//Magnetometer Registers
#define WHO_AM_I_AK8963  0x00 // should return 0x48
#define INFO             0x01
#define AK8963_ST1       0x02  // data ready status bit 0
#define AK8963_XOUT_L	   0x03  // data
#define AK8963_XOUT_H	   0x04
#define AK8963_YOUT_L	   0x05
#define AK8963_YOUT_H	   0x06
#define AK8963_ZOUT_L	   0x07
#define AK8963_ZOUT_H	   0x08
#define AK8963_ST2       0x09  // Data overflow bit 3 and data read error status bit 2
#define AK8963_CNTL      0x0A  // Power down (0000), single-measurement (0001), self-test (1000) and Fuse ROM (1111) modes on bits 3:0
#define AK8963_ASTC      0x0C  // Self test control
#define AK8963_I2CDIS    0x0F  // I2C disable
#define AK8963_ASAX      0x10  // Fuse ROM x-axis sensitivity adjustment value
#define AK8963_ASAY      0x11  // Fuse ROM y-axis sensitivity adjustment value
#define AK8963_ASAZ      0x12  // Fuse ROM z-axis sensitivity adjustment value

#define SELF_TEST_X_GYRO 0x00
#define SELF_TEST_Y_GYRO 0x01
#define SELF_TEST_Z_GYRO 0x02

#define SELF_TEST_X_ACCEL 0x0D
#define SELF_TEST_Y_ACCEL 0x0E
#define SELF_TEST_Z_ACCEL 0x0F

#define XG_OFFSET_H      0x13  // User-defined trim values for gyroscope
#define XG_OFFSET_L      0x14
#define YG_OFFSET_H      0x15
#define YG_OFFSET_L      0x16
#define ZG_OFFSET_H      0x17
#define ZG_OFFSET_L      0x18
#define SMPLRT_DIV       0x19
#define CONFIG           0x1A
#define GYRO_CONFIG      0x1B
#define ACCEL_CONFIG     0x1C
#define ACCEL_CONFIG2    0x1D
#define LP_ACCEL_ODR     0x1E
#define WOM_THR          0x1F

#define WHO_AM_I_MPU9250 0x75 // Should return 0x71
#define XA_OFFSET_H      0x06 // User-defined trim values for accelerometer
#define XA_OFFSET_L_TC   0x07
#define YA_OFFSET_H      0x08
#define YA_OFFSET_L_TC   0x09
#define ZA_OFFSET_H      0x0A
#define ZA_OFFSET_L_TC   0x0B
#define SELF_TEST_X      0x0D
#define SELF_TEST_Y      0x0E
#define SELF_TEST_Z      0x0F
#define SELF_TEST_A      0x10
#define XG_OFFS_USRL     0x14
#define XG_OFFS_USRH     0x15
#define YG_OFFS_USRH     0x15
#define YG_OFFS_USRL     0x16
#define ZG_OFFS_USRH     0x17
#define ZG_OFFS_USRL     0x18
#define SMPLRT_DIV       0x19
#define CONFIG           0x1A
#define GYRO_CONFIG      0x1B
#define ACCEL_CONFIG     0x1C
#define FIFO_EN          0x23
#define I2C_MST_CTRL     0x24
#define INT_PIN_CFG      0x37
#define INT_ENABLE       0x38
#define INT_STATUS       0x3A
#define ACCEL_XOUT_H     0x3B
#define GYRO_XOUT_H      0x43
#define TEMP_OUT_H       0x41
#define USER_CTRL        0x6A  // Bit 7 enable DMP, bit 3 reset DMP
#define PWR_MGMT_1       0x6B  // Device defaults to the SLEEP mode
#define PWR_MGMT_2       0x6C
#define FIFO_COUNTH      0x72
#define FIFO_R_W         0x74
#define WHO_AM_I_MPU6050 0x75 // Should return 0x68
#define MPU9250_ADDRESS  0x68
#define AK8963_ADDRESS   0x0C   //  Address of magnetometer
#define XA_OFFSET_H      0x77
#define XA_OFFSET_L      0x78
#define YA_OFFSET_H      0x7A
#define YA_OFFSET_L      0x7B
#define ZA_OFFSET_H      0x7D
#define ZA_OFFSET_L      0x7E

#define DEG_TO_RAD PI/180.0f
#define RAD_TO_DEG 180.0f/PI

#define AHRS true        // set to false for basic data read
#define SerialDebug true   // set to true to get Serial output for debugging
#define calibrateMagnetometer 0

#define offsetX 95
#define offsetY 90
#define offsetZ 100

// Set initial input parameters
enum Ascale {
  AFS_2G = 0,
  AFS_4G,
  AFS_8G,
  AFS_16G
};

enum Gscale {
  GFS_250DPS = 0,
  GFS_500DPS,
  GFS_1000DPS,
  GFS_2000DPS
};

enum Mscale {
  MFS_14BITS = 0, // 0.6 mG per LSB
  MFS_16BITS      // 0.15 mG per LSB
};

// PID
int consigneX, erreurX, somme_erreursX, variation_erreurX, erreur_precedenteX;
int consigneY, erreurY, somme_erreursY, variation_erreurY, erreur_precedenteY;
int consigneZ, erreurZ, somme_erreursZ, variation_erreurZ, erreur_precedenteZ;

// Specify sensor full scale
uint8_t Gscale = GFS_250DPS;
uint8_t Ascale = AFS_2G;
uint8_t Mscale = MFS_16BITS; // Choose either 14-bit or 16-bit magnetometer resolution
uint8_t Mmode = 0x06;        // 2 for 8 Hz, 6 for 100 Hz continuous magnetometer data read
float aRes, gRes, mRes;      // scale resolutions per LSB for the sensors

// Pin definitions
int intPin = 12;  // These can be changed, 2 and 3 are the Arduinos ext int pins

int16_t accelCount[3];  // Stores the 16-bit signed accelerometer sensor output
int16_t gyroCount[3];   // Stores the 16-bit signed gyro sensor output
int16_t magCount[3];    // Stores the 16-bit signed magnetometer sensor output

// global constants for 9 DoF fusion and AHRS (Attitude and Heading Reference System)
float GyroMeasError = PI * (40.0f / 180.0f);   // gyroscope measurement error in rads/s (start at 40 deg/s)
float GyroMeasDrift = PI * (0.0f  / 180.0f);   // gyroscope measurement drift in rad/s/s (start at 0.0 deg/s/s)

// There is a tradeoff in the beta parameter between accuracy and response speed.
// In the original Madgwick study, beta of 0.041 (corresponding to GyroMeasError of 2.7 degrees/s) was found to give optimal accuracy.
// However, with this value, the LSM9SD0 response time is about 10 seconds to a stable initial quaternion.
// Subsequent changes also require a longish lag time to a stable output, not fast enough for a quadcopter or robot car!
// By increasing beta (GyroMeasError) by about a factor of fifteen, the response time constant is reduced to ~2 sec
// I haven't noticed any reduction in solution accuracy. This is essentially the I coefficient in a PID control sense;
// the bigger the feedback coefficient, the faster the solution converges, usually at the expense of accuracy.
// In any case, this is the free parameter in the Madgwick filtering and fusion scheme.
float beta = sqrt(3.0f / 4.0f) * GyroMeasError;   // compute beta
float zeta = sqrt(3.0f / 4.0f) * GyroMeasDrift;   // compute zeta, the other free parameter in the Madgwick scheme usually set to a small or zero value

uint32_t delt_t = 0; // used to control display output rate
uint32_t count = 0, sumCount = 0; // used to control display output rate
float deltat = 0.0f, sum = 0.0f;        // integration interval for both filter schemes
uint32_t lastUpdate = 0, firstUpdate = 0; // used to calculate integration interval
uint32_t Now = 0;        // used to calculate integration interval

float ax, ay, az, gx, gy, gz, mx, my, mz; // variables to hold latest sensor data values
float q[4] = {1.0f, 0.0f, 0.0f, 0.0f};    // vector to hold quaternion
float pitch, yaw, roll;

#if(calibrateMagnetometer)
  int minX = 0;
  int maxX = 0;
  int minY = 0;
  int maxY = 0;
  int minZ = 0;
  int maxZ = 0;
  int offX = 0;
  int offY = 0;
  int offZ = 0;
#endif

float magSensitivity[3] = {0, 0, 0};
float magMax[3] = {190.0f, 331.0f, 45.0f};
float magMin[3] = {-205.0f, -41.0f, -347.0f};
float magbias[3] = {-7.0f, 145.0f, -151.0f};
float gyroBias[3] = {-0.3f, 1.0f, -1.0f};
float accelBias[3] = {0.024f, 0.030f, -0.024f};

float rawMagScale[3];
float magScale[3];
float avgMagScale;

// Create servos instances
Servo servo_X;
Servo servo_Y;
Servo servo_Z;

int initialisation = 1;

void setup()
{
  Wire.begin();
  //  TWBR = 12;  // 400 kbit/sec I2C speed
  Serial.begin(38400);

  // Read the WHO_AM_I register, this is a good test of communication
  byte c = readByte(MPU9250_ADDRESS, WHO_AM_I_MPU9250);  // Read WHO_AM_I register for MPU-9250

  delay(1000);

  if (c == 0x71) // WHO_AM_I should always be 0x68
  {
    Serial.println("MPU9250 is online...");

    // Initialize device for active mode read of acclerometer, gyroscope, and temperature
    initMPU9250();
    Serial.println("MPU9250 initialized for active data mode....");

    // Read WHO_AM_I register for AK8963. Should always be 0x48
    byte d = readByte(AK8963_ADDRESS, WHO_AM_I_AK8963);
    delay(1000);

    // Initialize device for active mode read of magnetometer
    initAK8963(magSensitivity);
    Serial.println("AK8963 initialized for active data mode....");
    Serial.println("Sensitivity values : ");
    Serial.print("X-Axis sensitivity adjustment value "); Serial.println(magSensitivity[0], 2);
    Serial.print("Y-Axis sensitivity adjustment value "); Serial.println(magSensitivity[1], 2);
    Serial.print("Z-Axis sensitivity adjustment value "); Serial.println(magSensitivity[2], 2);

  }
  else
  {
    Serial.print("Could not connect to MPU9250: 0x");
    Serial.println(c, HEX);
    while (1) ; // Loop forever if communication doesn't happen
  }

  // Initialisation
  somme_erreursX = (int(offsetX) << 7) / Ki_X;
  somme_erreursY = (int(offsetY) << 7) / Ki_Y;
  somme_erreursZ = (int(offsetZ) << 7) / Ki_Z;
  
  servo_X.attach(3); // horizontal - roll
  servo_Y.attach(6); // vertical - pitch
  servo_Z.attach(5); // transversal - yaw

  getAres();
  getGres();
  getMres();
  
}

void loop()
{
  #if(!calibrateMagnetometer)

    if (readByte(MPU9250_ADDRESS, INT_STATUS) & 0x01) {
      
      readAccelData(accelCount);  // Read the x/y/z adc values
      // Calculate the accleration value into actual g's
      ax = (float)accelCount[0] * aRes - accelBias[0]; // - 0.024
      ay = (float)accelCount[1] * aRes - accelBias[1]; // - 0.030
      az = (float)accelCount[2] * aRes - accelBias[2]; // + 0.024
  
      readGyroData(gyroCount);  // Read the x/y/z adc values
      // Calculate the gyro value into actual degrees per second
      gx = (float)gyroCount[0] * gRes - gyroBias[0]; // + 0.3
      gy = (float)gyroCount[1] * gRes - gyroBias[1]; // - 1.0
      gz = (float)gyroCount[2] * gRes - gyroBias[2]; // + 1.0
  
      readMagData(magCount);  // Read the x/y/z adc values
      // Calculate the magnetometer values in milliGauss
      mx = ( (float)magCount[0] * mRes * magSensitivity[0] - magbias[0] * mRes * magSensitivity[0] ) * magScale[0];
      my = ( (float)magCount[1] * mRes * magSensitivity[1] - magbias[1] * mRes * magSensitivity[1] ) * magScale[1];
      mz = ( (float)magCount[2] * mRes * magSensitivity[2] - magbias[2] * mRes * magSensitivity[2] ) * magScale[2];
    }
  
    Now = micros();
    deltat = ((Now - lastUpdate) / 1000000.0f); // set integration time by time elapsed since last filter update
    lastUpdate = Now;
  
    sum += deltat; // sum for averaging filter update rate
    sumCount++;
  
    MadgwickQuaternionUpdate(ax, ay, az, gx * DEG_TO_RAD, gy * DEG_TO_RAD, gz * DEG_TO_RAD,  my,  mx, -mz);
    //MadgwickQuaternionUpdate(ax, ay, az, gx * DEG_TO_RAD, gy * DEG_TO_RAD, gz * DEG_TO_RAD);
  
    if (!AHRS) {
  
        if (SerialDebug) {
          // Print acceleration values in milligs
          #if(0)
            Serial.print("X-acceleration: "); Serial.print(1000 * ax); Serial.print(" mg\t\t\t");
            Serial.print("Y-acceleration: "); Serial.print(1000 * ay); Serial.print(" mg\t\t\t");
            Serial.print("Z-acceleration: "); Serial.print(1000 * az); Serial.println(" mg");
          #endif
  
          // Print gyro values in degree/sec
          #if(0)
            Serial.print("X-gyro rate: "); Serial.print(gx, 3); Serial.print(" degrees/sec\t\t\t");
            Serial.print("Y-gyro rate: "); Serial.print(gy, 3); Serial.print(" degrees/sec\t\t\t");
            Serial.print("Z-gyro rate: "); Serial.print(gz, 3); Serial.println(" degrees/sec");
          #endif
  
          // Print mag values in degree/sec
          #if(1)
            Serial.print("X-mag field: "); Serial.print(mx); Serial.print(" mG\t\t\t");
            Serial.print("Y-mag field: "); Serial.print(my); Serial.print(" mG\t\t\t");
            Serial.print("Z-mag field: "); Serial.print(mz); Serial.println(" mG");
          #endif
  
        }
  
    }
    else {
    
      delt_t = millis() - count;

      yaw   = atan2(2.0f * (q[1] * q[2] + q[0] * q[3]), q[0] * q[0] + q[1] * q[1] - q[2] * q[2] - q[3] * q[3]);
      pitch = -asin(2.0f * (q[1] * q[3] - q[0] * q[2]));
      roll  = atan2(2.0f * (q[0] * q[1] + q[2] * q[3]), q[0] * q[0] - q[1] * q[1] - q[2] * q[2] + q[3] * q[3]);
      
      pitch *= RAD_TO_DEG;
      yaw   *= RAD_TO_DEG;
      roll  *= RAD_TO_DEG;
  
      Serial.print("Yaw, Pitch, Roll: ");
      Serial.print(yaw, 2);
      Serial.print(", ");
      Serial.print(pitch, 2);
      Serial.print(", ");
      Serial.println(roll, 2);
  
      //Serial.print("rate = "); Serial.print((float)sumCount / sum, 2); Serial.println(" Hz");
  
      count = millis();
      sumCount = 0;
      sum = 0;

      if ( initialisation == 1 && ( (yaw < 1.0 && yaw > -1.0) && (pitch < 1.0 && pitch > -1.0) || (roll < 1.0 && roll > -1.0) ) )  {
        // Fin initialisation
        initialisation = 0;
      }
      
      if ( initialisation == 0 ) {
        computeOrder();
        updatePO();
      }
  
    }
  #else
    // Read the x/y/z adc values
    readMagData(magCount);

    mx = (float)magCount[0];
    my = (float)magCount[1];
    mz = (float)magCount[2];
    
    // Determine Min / Max values
    if (mx < minX) minX = mx;
    if (mx > maxX) maxX = mx;
    if (my < minY) minY = my;
    if (my > maxY) maxY = my;
    if (mz < minZ) minZ = mz;
    if (mz > maxZ) maxZ = mz;
  
    // Calculate offsets
    offX = (maxX + minX)/2;
    offY = (maxY + minY)/2;
    offZ = (maxZ + minZ)/2;

    Serial.print(minX);
    Serial.print(" : ");
    Serial.print(maxX);
    Serial.print(" : ");
    Serial.print(minY);
    Serial.print(" : ");
    Serial.print(maxY);
    Serial.print(" : ");
    Serial.print(minZ);
    Serial.print(" : ");
    Serial.print(maxZ);
    Serial.print(" ----- ");
    
    Serial.print(offX);
    Serial.print(" : ");
    Serial.print(offY);
    Serial.print(" : ");
    Serial.println(offZ);

    // -205 : 190 : -41 : 331 : -347 : 45 ----- -7 : 145 : -151

  #endif
}

void updatePO() {

  servo_X.write(consigneX);
  servo_Y.write(consigneY);
  servo_Z.write(consigneZ);
}

void computeOrder() {

  // Correction PID sur X
  erreurX = pitch;
  somme_erreursX += erreurX;
  variation_erreurX = erreurX - erreur_precedenteX;
  consigneX = Kp_X * erreurX + Ki_X * somme_erreursX + Kd_X * variation_erreurX;
  erreur_precedenteX = erreurX;
  consigneX = consigneX >> 7;

  // Correction PID sur Y
  erreurY = roll;
  somme_erreursY += erreurY;
  variation_erreurY = erreurY - erreur_precedenteY;
  consigneY = Kp_Y * erreurY + Ki_Y * somme_erreursY + Kd_Y * variation_erreurY;
  erreur_precedenteY = erreurY;
  consigneY = consigneY >> 7;

  // Correction PID sur Z
  erreurZ = yaw;
  somme_erreursZ += erreurZ;
  variation_erreurZ = erreurZ - erreur_precedenteZ;
  consigneZ = Kp_Z * erreurZ + Ki_Z * somme_erreursZ + Kd_Z * variation_erreurZ;
  erreur_precedenteZ = erreurZ;
  consigneZ = consigneZ >> 7;
}

//===================================================================================================================
//====== Set of useful function to access acceleration. gyroscope, magnetometer, and temperature data
//===================================================================================================================

void getMres() {
  switch (Mscale)
  {
    // Possible magnetometer scales (and their register bit settings) are:
    // 14 bit resolution (0) and 16 bit resolution (1)
    case MFS_14BITS:
      mRes = 10.*4912. / 8190.; // Proper scale to return milliGauss
      break;
    case MFS_16BITS:
      mRes = 10.*4912. / 32760.0; // Proper scale to return milliGauss
      break;
  }
}

void getGres() {
  switch (Gscale)
  {
    // Possible gyro scales (and their register bit settings) are:
    // 250 DPS (00), 500 DPS (01), 1000 DPS (10), and 2000 DPS  (11).
    // Here's a bit of an algorith to calculate DPS/(ADC tick) based on that 2-bit value:
    case GFS_250DPS:
      gRes = 250.0 / 32768.0;
      break;
    case GFS_500DPS:
      gRes = 500.0 / 32768.0;
      break;
    case GFS_1000DPS:
      gRes = 1000.0 / 32768.0;
      break;
    case GFS_2000DPS:
      gRes = 2000.0 / 32768.0;
      break;
  }
}

void getAres() {
  switch (Ascale)
  {
    // Possible accelerometer scales (and their register bit settings) are:
    // 2 Gs (00), 4 Gs (01), 8 Gs (10), and 16 Gs  (11).
    // Here's a bit of an algorith to calculate DPS/(ADC tick) based on that 2-bit value:
    case AFS_2G:
      aRes = 2.0 / 32768.0;
      break;
    case AFS_4G:
      aRes = 4.0 / 32768.0;
      break;
    case AFS_8G:
      aRes = 8.0 / 32768.0;
      break;
    case AFS_16G:
      aRes = 16.0 / 32768.0;
      break;
  }
}

void readAccelData(int16_t * destination)
{
  uint8_t rawData[6];  // x/y/z accel register data stored here
  readBytes(MPU9250_ADDRESS, ACCEL_XOUT_H, 6, &rawData[0]);  // Read the six raw data registers into data array
  destination[0] = ((int16_t)rawData[0] << 8) | rawData[1] ;  // Turn the MSB and LSB into a signed 16-bit value
  destination[1] = ((int16_t)rawData[2] << 8) | rawData[3] ;
  destination[2] = ((int16_t)rawData[4] << 8) | rawData[5] ;
}


void readGyroData(int16_t * destination)
{
  uint8_t rawData[6];  // x/y/z gyro register data stored here
  readBytes(MPU9250_ADDRESS, GYRO_XOUT_H, 6, &rawData[0]);  // Read the six raw data registers sequentially into data array
  destination[0] = ((int16_t)rawData[0] << 8) | rawData[1] ;  // Turn the MSB and LSB into a signed 16-bit value
  destination[1] = ((int16_t)rawData[2] << 8) | rawData[3] ;
  destination[2] = ((int16_t)rawData[4] << 8) | rawData[5] ;
}

void readMagData(int16_t * destination)
{
  uint8_t rawData[7];  // x/y/z gyro register data, ST2 register stored here, must read ST2 at end of data acquisition
  if (readByte(AK8963_ADDRESS, AK8963_ST1) & 0x01) { // wait for magnetometer data ready bit to be set
    readBytes(AK8963_ADDRESS, AK8963_XOUT_L, 7, &rawData[0]);  // Read the six raw data and ST2 registers sequentially into data array
    uint8_t c = rawData[6]; // End data read by reading ST2 register
    if (!(c & 0x08)) { // Check if magnetic sensor overflow set, if not then report data
      destination[0] = ((int16_t)rawData[1] << 8) | rawData[0] ;  // Turn the MSB and LSB into a signed 16-bit value
      destination[1] = ((int16_t)rawData[3] << 8) | rawData[2] ;  // Data stored as little Endian
      destination[2] = ((int16_t)rawData[5] << 8) | rawData[4] ;
    }
  }
}

void initAK8963(float * destination /* magCalibration */)
{
  // First extract the factory calibration for each magnetometer axis
  uint8_t rawData[3];  // x/y/z gyro calibration data stored here
  writeByte(AK8963_ADDRESS, AK8963_CNTL, 0x00); // Power down magnetometer
  delay(10);
  writeByte(AK8963_ADDRESS, AK8963_CNTL, 0x0F); // Enter Fuse ROM access mode
  delay(10);
  readBytes(AK8963_ADDRESS, AK8963_ASAX, 3, &rawData[0]);  // Read the x-, y-, and z-axis calibration values
  destination[0] =  (float)(rawData[0] - 128) / 256. + 1.; // Return x-axis sensitivity adjustment values, etc.
  destination[1] =  (float)(rawData[1] - 128) / 256. + 1.;
  destination[2] =  (float)(rawData[2] - 128) / 256. + 1.;
  writeByte(AK8963_ADDRESS, AK8963_CNTL, 0x00); // Power down magnetometer
  delay(10);
  
  // Configure the magnetometer for continuous read and highest resolution
  // set Mscale bit 4 to 1 (0) to enable 16 (14) bit resolution in CNTL register,
  // and enable continuous mode data acquisition Mmode (bits [3:0]), 0010 for 8 Hz and 0110 for 100 Hz sample rates
  writeByte(AK8963_ADDRESS, AK8963_CNTL, Mscale << 4 | Mmode); // Set magnetometer data resolution and sample ODR
  delay(10);

  rawMagScale[0] = (magMax[0] - magMin[0]) / 2;
  rawMagScale[1] = (magMax[1] - magMin[1]) / 2;
  rawMagScale[2] = (magMax[2] - magMin[2]) / 2;
  avgMagScale = (rawMagScale[0] + rawMagScale[1] + rawMagScale[2]) / 3;
  magScale[0] = avgMagScale / rawMagScale[0];
  magScale[1] = avgMagScale / rawMagScale[1];
  magScale[2] = avgMagScale / rawMagScale[2];
}


void initMPU9250()
{
  // Reset accel offset 
  writeByte(MPU9250_ADDRESS, XA_OFFSET_H, 0x00);
  writeByte(MPU9250_ADDRESS, XA_OFFSET_L, 0x00);
  writeByte(MPU9250_ADDRESS, YA_OFFSET_H, 0x00);
  writeByte(MPU9250_ADDRESS, YA_OFFSET_L, 0x00);
  writeByte(MPU9250_ADDRESS, ZA_OFFSET_H, 0x00);
  writeByte(MPU9250_ADDRESS, ZA_OFFSET_L, 0x00);

  // Reset accel offset
  writeByte(MPU9250_ADDRESS, XG_OFFS_USRL, 0x00);
  writeByte(MPU9250_ADDRESS, XG_OFFS_USRH, 0x00);
  writeByte(MPU9250_ADDRESS, YG_OFFS_USRL, 0x00);
  writeByte(MPU9250_ADDRESS, YG_OFFS_USRH, 0x00);
  writeByte(MPU9250_ADDRESS, ZG_OFFS_USRL, 0x00);
  writeByte(MPU9250_ADDRESS, ZG_OFFS_USRH, 0x00);

  // Reset device, clear sleep mode, use internal oscillator
  writeByte(MPU9250_ADDRESS, PWR_MGMT_1, 0x80);
  // Enable all sensors
  writeByte(MPU9250_ADDRESS, PWR_MGMT_2, 0x00);

  delay(200);

  // Set sample rate = gyroscope output rate/(1 + SMPLRT_DIV)
  writeByte(MPU9250_ADDRESS, SMPLRT_DIV, 0x04);  // Use a 200 Hz rate; a rate consistent with the filter update rate

  // Set gyroscope full scale range
  writeByte(MPU9250_ADDRESS, GYRO_CONFIG, 0x00);
  // Set accelerometer full-scale range configuration
  writeByte(MPU9250_ADDRESS, ACCEL_CONFIG, 0x00);

  writeByte(MPU9250_ADDRESS, INT_PIN_CFG, 0x22);
  writeByte(MPU9250_ADDRESS, INT_ENABLE, 0x01);  // Enable data ready (bit 0) interrupt
  delay(100);
}

// Wire.h read and write protocols
void writeByte(uint8_t address, uint8_t subAddress, uint8_t data)
{
  Wire.beginTransmission(address);  // Initialize the Tx buffer
  Wire.write(subAddress);           // Put slave register address in Tx buffer
  Wire.write(data);                 // Put data in Tx buffer
  Wire.endTransmission();           // Send the Tx buffer
}
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

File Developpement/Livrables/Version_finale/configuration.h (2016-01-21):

/* Adresse des capteurs sur le bus i2c */
#define MPU9250_CAM_ADDRESS   0x68
#define AK8963_ADDRESS        0x0C

/* Definition des numeros de sortie des moteurs sur le microcontroleur */
#define YAW_MOTOR_P1      9
#define YAW_MOTOR_P2      6
#define YAW_MOTOR_P3      10
#define YAW_MOTOR_EN      8

#define PITCH_MOTOR_P1    20
#define PITCH_MOTOR_P2    21
#define PITCH_MOTOR_P3    22
#define PITCH_MOTOR_EN    15

#define ROLL_MOTOR_P1     3
#define ROLL_MOTOR_P2     4
#define ROLL_MOTOR_P3     5
#define ROLL_MOTOR_EN     7

/* Sens de rotation des moteurs */
#define SENS_MOTOR_YAW          -1
#define SENS_MOTOR_PITCH        -1
#define SENS_MOTOR_ROLL         -1

/* Constantes liees au capteur MPU-9250 */
#define ACC_RESOLUTION   (2.0 / 32768.0)          /* Resolution de l'accelerometre */
#define GYRO_RESOLUTION  (250.0 / 32768.0)        /* Resolution du gyroscope */
#define MAG_RESOLUTION   1.5    /* Resolution du magnetometre */

/* Valeurs de sensibilité du magnétomètre (ASAX, ASAY, ASAZ) */
#define AK8963_SENS_ASAX  1.11
#define AK8963_SENS_ASAY  1.07
#define AK8963_SENS_ASAZ  1.50

/* Adresses memoire EEPROM pour le stockage des donnees de calibration */
#define ADDR_GYRO_CAM_BIAS      0   /* 3 float */
#define ADDR_ACC_CAM_BIAS       12  /* 3 float */
#define ADD_MAG_CAM_BIAS        24  /* 3 float */
#define ADD_MAG_CAM_SCALE       36  /* 3 float */
#define FIRST_CALIBRATION_FLAG  60  /* 1 int */

#define ADDR_KP_PARAMETERS      70  /* 3 float : Yaw, Pitch, Roll */
#define ADDR_KI_PARAMETERS      82  /* 3 float : Yaw, Pitch, Roll */
#define ADDR_KD_PARAMETERS      94  /* 3 float : Yaw, Pitch, Roll */
#define ADDR_INTERRUPT_VALUES   106 /* 3 int */

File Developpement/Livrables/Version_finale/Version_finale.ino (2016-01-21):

#include <Wire.h>
#include <EEPROM.h>

#include "types.h"
#include "parameters.h"
#include "configuration.h"
#include "registers_map.h"

/* Permet d'activer ou de desactiver le mode debug et les prints */
#define DEBUG                 1

#define PRINT_RAW_VALUES      0     /* Permet d'afficher les valeurs brutes du capteur */
#define PRINT_YPR_VALUES      0     /* Permet d'afficher les valeurs de angles Yaw, Pitch, Roll */

#define PRINT_PID_COMPUTING   0     /* Permet d'afficher les composants du calcul du PID */
#define AXE_TO_PRINT          0     /* Permet de selectionner l'axe a afficher pour le PID (0 : Yaw, 1 : Pitch, 2 : Roll) */

#define LOCK_YAW              0

/* --------------------------------------------------------------- */
/* ---------------------- Variables partagess -------------------- */
/* --------------------------------------------------------------- */

/* Active ou desactive les axes correspondants */
int enableYaw   = 1;
int enablePitch = 1;
int enableRoll  = 1;

/* Parametres pour la frequence des interruptions */
long PIT_LDVAL_freq[4];
long PIT_LDVAL_value[4];

/* Variables pour la gestion des donnes recues depuis la console de configuration */
int nbOctets = 0;
char data[32];

float offset[3] = {0.0, 0.0, 0.0};

/* Lookup table pour la commande des moteurs */
/* Les moteurs utilises contiennent 7 trinomes d'enroulements */
const int pwmSin[] = {128, 132, 136, 140, 143, 147, 151, 155, 159, 162, 166, 170, 174, 178, 181, 185, 189, 192, 196, 200, 203, 207, 211, 214, 218, 221, 225, 228, 232, 235, 238, 239, 240, 241, 242, 243, 244, 245, 246, 247, 248, 248, 249, 250, 250, 251, 252, 252, 253, 253, 253, 254, 254, 254, 255, 255, 255, 255, 255, 255, 255, 255, 255, 255, 255, 255, 255, 254, 254, 254, 253, 253, 253, 252, 252, 251, 250, 250, 249, 248, 248, 247, 246, 245, 244, 243, 242, 241, 240, 239, 238, 239, 240, 241, 242, 243, 244, 245, 246, 247, 248, 248, 249, 250, 250, 251, 252, 252, 253, 253, 253, 254, 254, 254, 255, 255, 255, 255, 255, 255, 255, 255, 255, 255, 255, 255, 255, 254, 254, 254, 253, 253, 253, 252, 252, 251, 250, 250, 249, 248, 248, 247, 246, 245, 244, 243, 242, 241, 240, 239, 238, 235, 232, 228, 225, 221, 218, 214, 211, 207, 203, 200, 196, 192, 189, 185, 181, 178, 174, 170, 166, 162, 159, 155, 151, 147, 143, 140, 136, 132, 128, 124, 120, 116, 113, 109, 105, 101, 97, 94, 90, 86, 82, 78, 75, 71, 67, 64, 60, 56, 53, 49, 45, 42, 38, 35, 31, 28, 24, 21, 18, 17, 16, 15, 14, 13, 12, 11, 10, 9, 8, 8, 7, 6, 6, 5, 4, 4, 3, 3, 3, 2, 2, 2, 1, 1, 1, 1, 1, 1, 1, 1, 1, 1, 1, 1, 1, 2, 2, 2, 3, 3, 3, 4, 4, 5, 6, 6, 7, 8, 8, 9, 10, 11, 12, 13, 14, 15, 16, 17, 18, 17, 16, 15, 14, 13, 12, 11, 10, 9, 8, 8, 7, 6, 6, 5, 4, 4, 3, 3, 3, 2, 2, 2, 1, 1, 1, 1, 1, 1, 1, 1, 1, 1, 1, 1, 1, 2, 2, 2, 3, 3, 3, 4, 4, 5, 6, 6, 7, 8, 8, 9, 10, 11, 12, 13, 14, 15, 16, 17, 18, 21, 24, 28, 31, 35, 38, 42, 45, 49, 53, 56, 60, 64, 67, 71, 75, 78, 82, 86, 90, 94, 97, 101, 105, 109, 113, 116, 120, 124};

/* Taille de la lookup table doit etre calculee au demarrage */
int sineArraySize;

/* Plage de valeurs pour 1 enroulement de trinome d'enroulements. (Taille de la lookup table divise par 3) */
int phaseShift;

/* Structure pour le traitement de l'asservissement PID */
t_PID ypr[3];

/* Structure pour la gestion de chaque moteur brushless */
t_motor brushless[3];

/* Structure pour la gestion du capteur */
t_IMU capteurCam;

/* Integration pour le filtre de Madgwick */
uint32_t lastUpdate = 0, Now = 0;
float deltat = 0.0;

/* Variables globales pour l'algorithme de Madgwick */
float GyroMeasError = PI * (40.0f / 180.0f);
float GyroMeasDrift = PI * (0.0f  / 180.0f);
float beta = sqrt(3.0f / 4.0f) * GyroMeasError;
float zeta = sqrt(3.0f / 4.0f) * GyroMeasDrift;

void setup()
{
  configInputsOutputs();

  configMotors();
  
  /* Demarrage et initialisation du capteur */
  delay(2000);
  
  Wire.begin();
  Serial.begin(115200);
  
  /* Variable locale */
  int calibrationDone;
  
  if (testComCapteur(MPU9250_CAM_ADDRESS) == 0)
  {
    initMPU9250(MPU9250_CAM_ADDRESS);
    initAK8963(MPU9250_CAM_ADDRESS, &capteurCam);
  }
  else
  {
    #if (DEBUG)
    Serial.println("Erreur communication i2c");
    #endif
    while(1);
  }

  /* Permet d'effectuer la calibration du capteur si elle n'a pas ete effectuee */
  calibrationDone = checkCalibration();

  if (calibrationDone != 1)
  {
    /* Calibration du gyroscope et de l'accelerometre du capteur */
    gyroAccCalibration( MPU9250_CAM_ADDRESS,
                        ADDR_GYRO_CAM_BIAS, ADDR_ACC_CAM_BIAS,
                        &capteurCam);
    
    /* Calibration du magnetometre du capteur de la camera */
    magCalibration( MPU9250_CAM_ADDRESS,
                    ADD_MAG_CAM_BIAS, ADD_MAG_CAM_SCALE,
                    &capteurCam);
    
    calibrationDone = 1;
    EEPROM.put(FIRST_CALIBRATION_FLAG, calibrationDone);
  }

  /* Chargement des parametres du gyroscope et de l'accelerometre */
  loadGyroAccCalibrationBias( ADDR_GYRO_CAM_BIAS, ADDR_ACC_CAM_BIAS,
                              capteurCam.gyroBias, capteurCam.accBias);

  /* Chargement des parametres du magnetometre */
  loadMagCalibrationData( ADD_MAG_CAM_BIAS, ADD_MAG_CAM_SCALE,
                          capteurCam.magBias, capteurCam.magScale);

  #if (DEBUG)
    printSensorValues(capteurCam);
  #endif

  getFirstOrientations(MPU9250_CAM_ADDRESS, AK8963_ADDRESS, &capteurCam);

  loadInitialParameters();

  configPID();

  //loadParameters();

  configInterrupts();

  deltat = 1 / (float)MADGWICK_FREQUENCY;
}

void loop()
{
  //plot(capteurCam.ypr[0], capteurCam.ypr[1], capteurCam.ypr[2], ypr[0].consigne, ypr[1].consigne, ypr[2].consigne);

  receiveDataFromConsole();

  #if (PRINT_PID_COMPUTING)
  
  Serial.print(ypr[AXE_TO_PRINT].consigne);
  Serial.print(" = ");
  Serial.print(ypr[AXE_TO_PRINT].kp);
  Serial.print(" * ");
  Serial.print(ypr[AXE_TO_PRINT].erreur);
  Serial.print(" + ");
  Serial.print(ypr[AXE_TO_PRINT].ki);
  Serial.print(" * ");
  Serial.print(ypr[AXE_TO_PRINT].sommeErreurs);
  Serial.print(" + ");
  Serial.print(ypr[AXE_TO_PRINT].kd);
  Serial.print(" * ");
  Serial.println(ypr[AXE_TO_PRINT].variationErreur);
  
  #endif

}

/* --------------------------------------------------------------- */
/* ----------------- Gestion de l'interruption 0 ----------------- */
/* --------------------------------------------------------------- */
void pit0_isr
(
  /* Ne prend pas de parametres */
)
{
  /* Recuperation des donnees brutes du capteur */
  getOrientation(MPU9250_CAM_ADDRESS, &capteurCam);

  /* Conversion de l'orientation sous forme de representation Euler */
  getYawPitchRoll(&capteurCam);
  
  PIT_TFLG0 = 1;
}
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

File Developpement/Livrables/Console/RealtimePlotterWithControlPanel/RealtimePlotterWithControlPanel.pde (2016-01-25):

// import libraries
import java.awt.Frame;
import java.awt.BorderLayout;
import controlP5.*; // http://www.sojamo.de/libraries/controlP5/
import processing.serial.*;

/* SETTINGS BEGIN */

// Serial port to connect to
String serialPortName = "/dev/tty.usbmodem1023821";

// If you want to debug the plotter without using a real serial port set this to true
boolean mockupSerial = true;

/* SETTINGS END */

Serial serialPort; // Serial port object

// interface stuff
ControlP5 cp5;
ControlFrame cf;

// Settings for the plotter are saved in this file
JSONObject plotterConfigJSON;

// plots
Graph BarChart = new Graph(225, 70, 600, 150, color(20, 20, 200));
Graph LineGraph = new Graph(225, 350, 600, 200, color (20, 20, 200));
float[] barChartValues = new float[6];
float[][] lineGraphValues = new float[6][100];
float[] lineGraphSampleNumbers = new float[100];
color[] graphColors = new color[6];

// helper for saving the executing path
String topSketchPath = "";

void setup() {
  frame.setTitle("Realtime plotter");
  size(890, 620);

  // set line graph colors
  graphColors[0] = color(131, 255, 20);
  graphColors[1] = color(232, 158, 12);
  graphColors[2] = color(255, 0, 0);
  graphColors[3] = color(62, 12, 232);
  graphColors[4] = color(13, 255, 243);
  graphColors[5] = color(200, 46, 232);

  // settings save file
  topSketchPath = sketchPath;
  plotterConfigJSON = loadJSONObject(topSketchPath+"/plotter_config.json");
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

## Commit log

2015-10-23 Modification structure et mises en plan pour version finale
    [Bielle pitch.SLDDRW, Bielle pitch.SLDPRT, Bielle roll.SLDDRW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]
2016-01-21 Version finale 3 axes
    [configuration.h]
2016-01-21 Mise à jour des livrables
    [Batterie.SLDPRT, Bielle pitch.SLDDRW, Bielle pitch.SLDPRT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]
2016-01-25 Ajout de la console de parametrage
2016-02-05 Ajout de la documentation du projet
2016-02-06 Ajout du répertoire pour la cross-compilation
2016-02-06 Ajout du lien pour la cross-compilation
2016-02-06 Ajout des Datasheets, photos et mise à jour du README
